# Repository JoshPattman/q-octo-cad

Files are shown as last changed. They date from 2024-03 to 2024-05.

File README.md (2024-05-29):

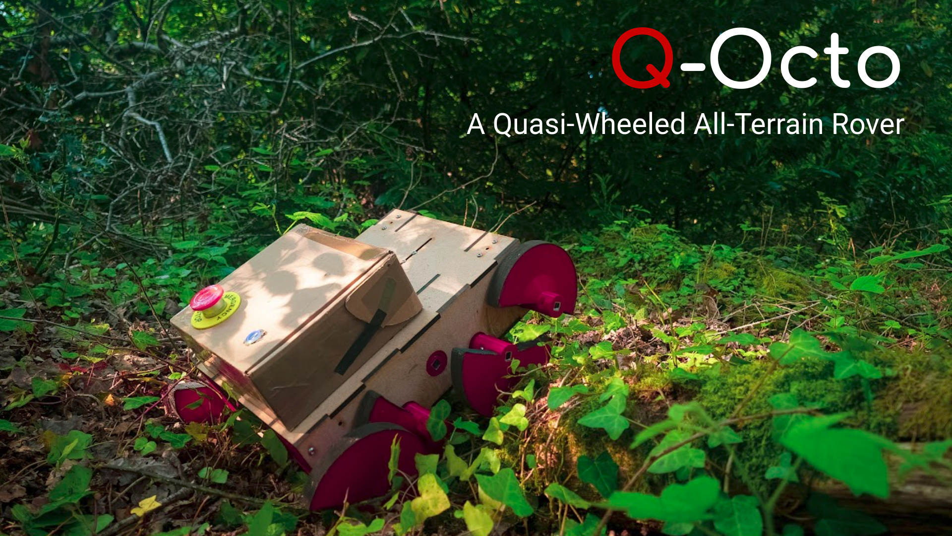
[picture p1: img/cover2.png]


# Q-Octo CAD
This Repo is the official home of the design of the Q-Octo robot! All CAD is using `FreeCAD Link Branch 2024-01-23`, but STL and DXF files are also provided.

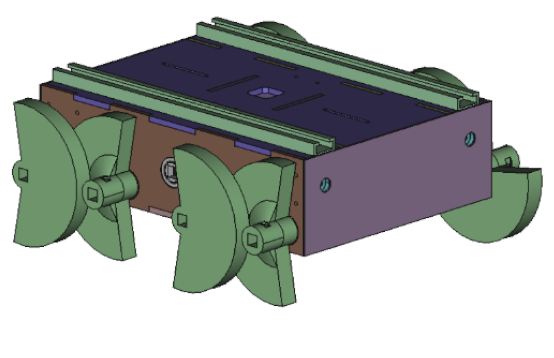
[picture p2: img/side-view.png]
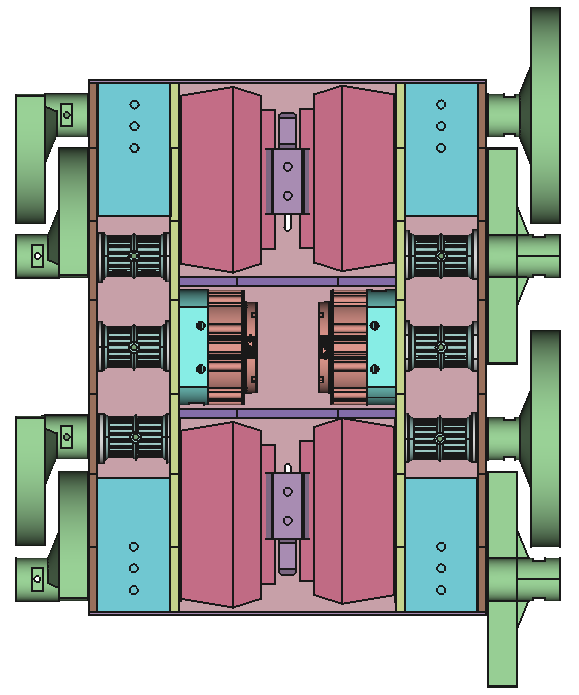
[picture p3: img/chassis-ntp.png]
 

## About Q-Octo
[Q-Octo](https://www.youtube.com/watch?v=2PIdxYJO_Ck) is an eight-quasi-wheeled robotics platform. It is designed to excel at forest traversal, easily being able to clamber over small logs and rocks due to its uniquely shaped wheels. However, due to each pair of neighboring wheels being 180 degrees out of phase, the robot can run smoothly as if it had circular wheels when on flat ground.

Q-Octo uses a pair of [CyberGear MicroMotors](https://www.aliexpress.com/item/1005005997659365.html), which provide not only high torque and speed but also feedback such as current amp draw and position. To power the motors, 4 [Parkside X20V](https://parkside-diy.com/gb/battery-technology/x20v-team) drill batteries are used, providing 6-hour continuous runtime paired with robust and safe recharging.

To build a Q-Octo, both a 3D printer and a laser cutter are required. It is sufficient to manufacture all 3D printed parts out of [Esun PLA+](https://www.esun3d.com/pla-pro-product/), providing excellent durability. All laser-cut parts (*except the front and rear battery cover) can be cut from 6 mm thick plyboard, which provides adequate rigidity and durability, assuming it is coated in outdoor paint.

## File Structure
- `cad/part/`: Contains all part files
- `cad/asm/`: Contains assembly files, using parts from `cad/part/`
- `mf/3d-print`: Contains all `stl` files ready for 3D printing
- `mf/lasercut`: Contains `dxf` files for laser-cutting

## Parts List _(Incomplete at current time)_

### Parts to Purchase
> These are just the mechanical parts for building the chassis. All of the control electronics can be found in the electronic repo.
- 2x CyberGear MicroMotor (Robot Dog Motor)
- 12mm Square Tube, Aluminum, Hollow (~1 meter, you need to cut it yourself)
- Assorted M4 bolts, ideally low profile
- M4 threaded inserts, diameter 5.6mm
- 20x 61704 ball bearings (20x27x4mm)
- 4x 5mm HTD belts 285mm length, 15mm wide
- 4x 5mm HTD belts 225mm length, 15mm wide
- 4x Parkside X20V drill battery

### Parts to Lasercut
> All parts should be lasercut from a 6mm wide material (unless otherwise specified), plyboard should be strong enough. It is recommended not to use acrylic as it can be brittle.
- 2x dxf/ChassisInnerPlate.dxf
- 2x dxf/ChassisOuterPlate.dxf
- 1x dxf/ChassisUpperPlate.dxf
- 1x dxf/ChassisLowerPlate.dxf
- 2x dxf/ChassisMotorSplashPlate.dxf
- 2x dxf/ChassisBatterySplashPlate.dxf (Cut this from thinner material, the thinner the better as it is not structural)

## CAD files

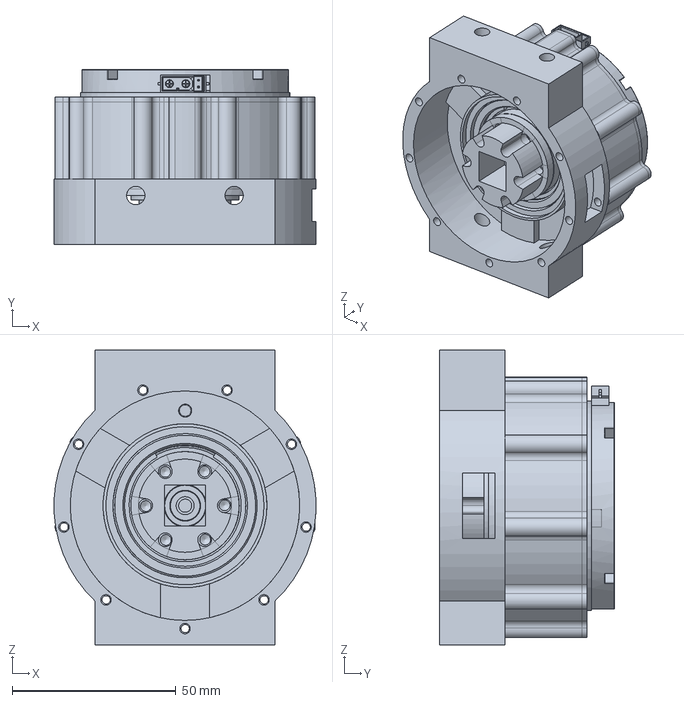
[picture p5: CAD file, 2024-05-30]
cad/asm/mounted-motor.FCStd
79.9 x 53.5 x 90.0 mm

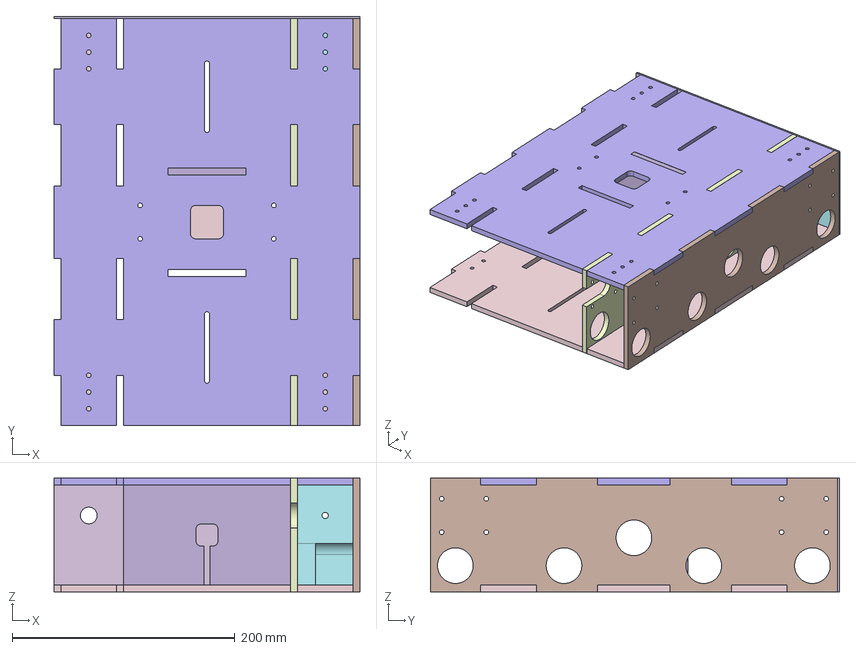
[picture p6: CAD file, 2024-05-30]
cad/part/chassis.FCStd
274.3 x 367.0 x 102.0 mm
LowerPlate
UpperPlate
OuterPlate
InnerPlate
PulleyBrace
MotorSplashPlate
BatterySplashPlate

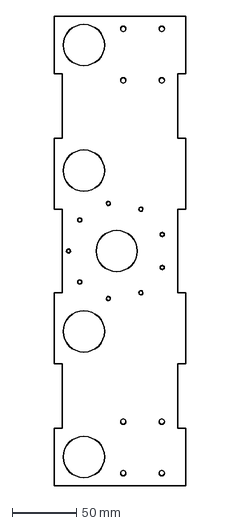
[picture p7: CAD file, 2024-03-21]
dxf/ChassisInnerPlate.dxf
102.0 x 365.0 mm

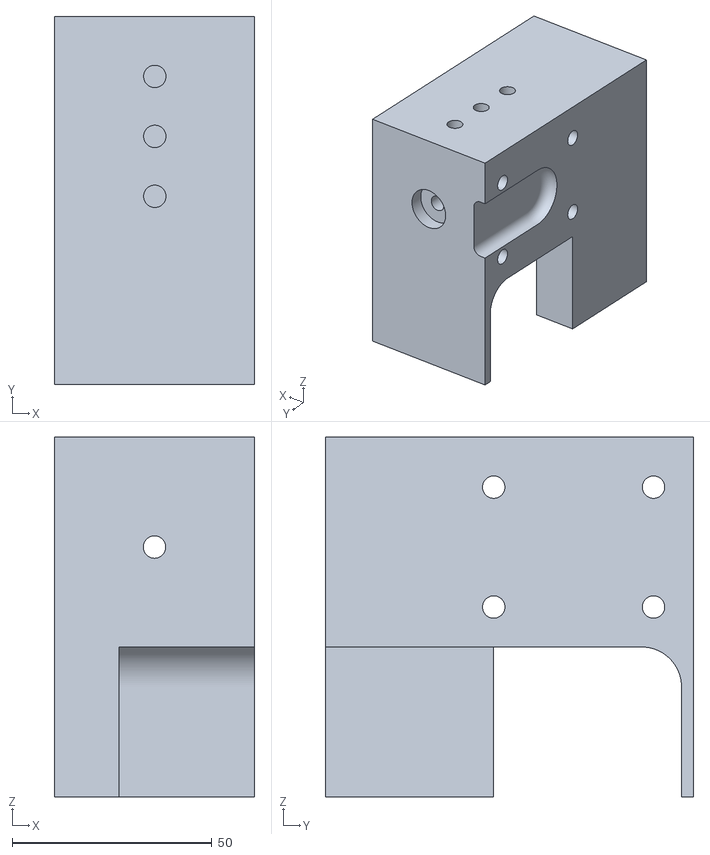
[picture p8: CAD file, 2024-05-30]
mf/3d-print/PulleyBrace.stl
50.1 x 92.1 x 90.0

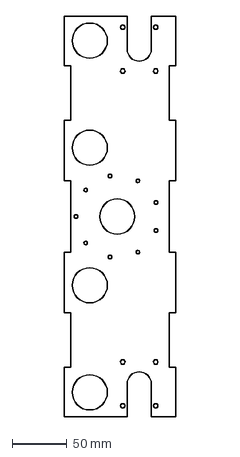
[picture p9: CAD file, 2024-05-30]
mf/lasercut/InnerPlate.dxf
102.0 x 365.0 mm

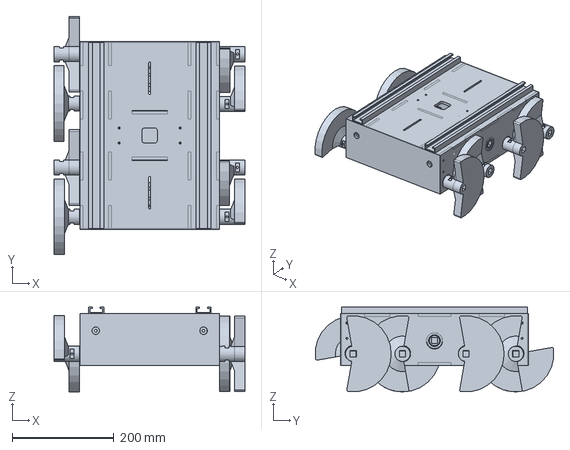
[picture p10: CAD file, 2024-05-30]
cad/asm/robot.FCStd
375.8 x 469.1 x 167.1 mm

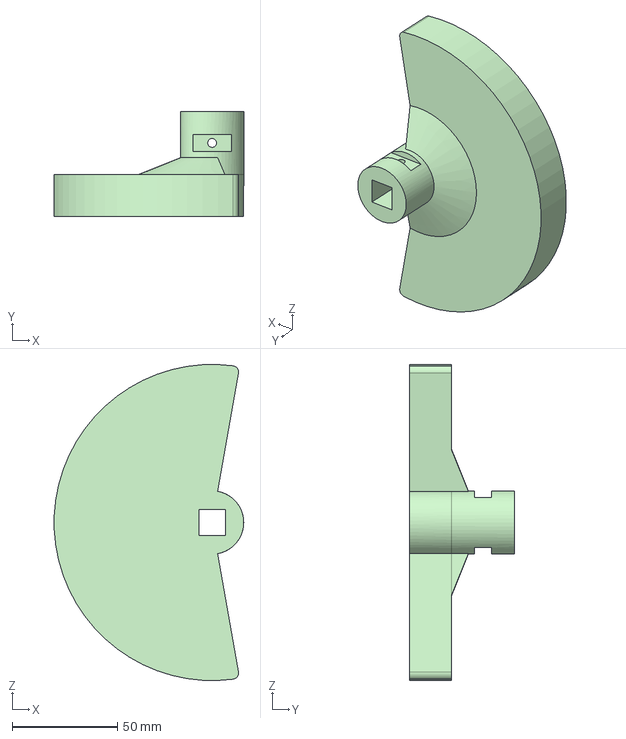
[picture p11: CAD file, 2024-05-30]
cad/part/wheel.FCStd
89.9 x 50.0 x 149.9 mm

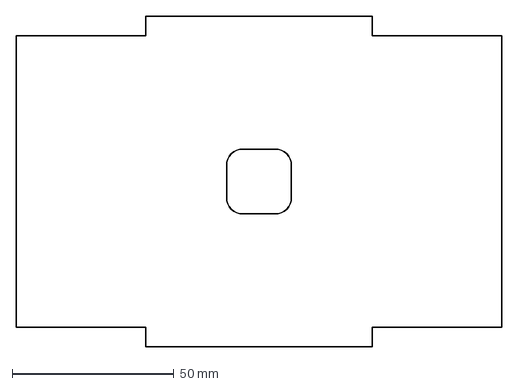
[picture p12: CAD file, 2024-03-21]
dxf/ChassisMotorSplashPlate.dxf
150.0 x 102.0 mm

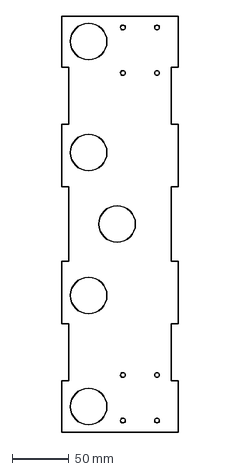
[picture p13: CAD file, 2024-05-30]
mf/lasercut/OuterPlate.dxf
102.0 x 365.0 mm

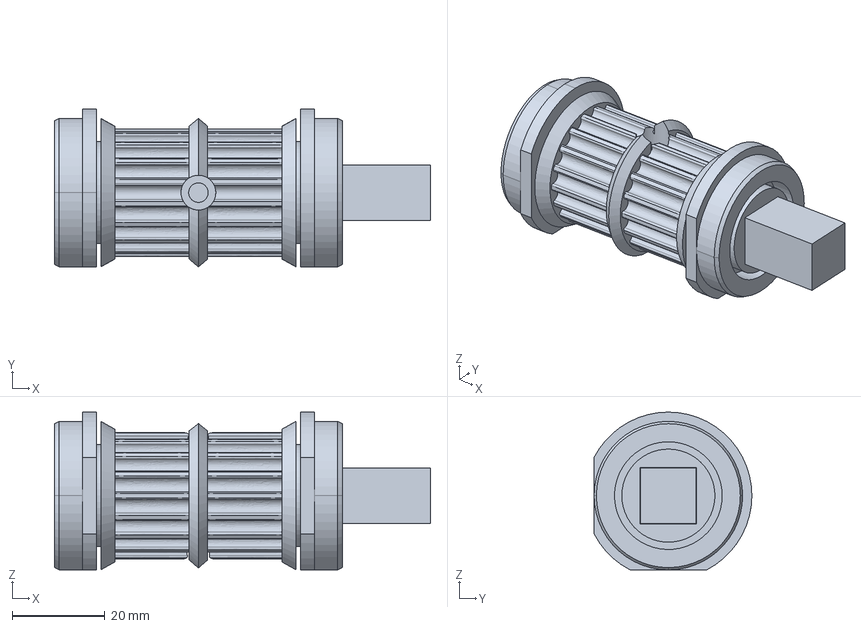
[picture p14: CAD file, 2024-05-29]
cad/asm/pulley.FCStd
81.0 x 34.0 x 34.0 mm

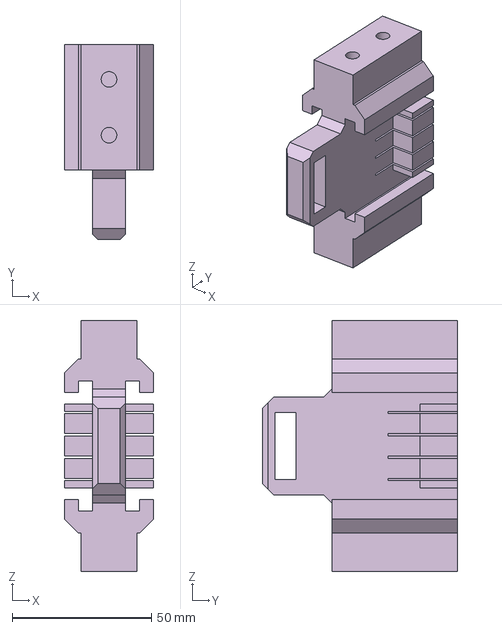
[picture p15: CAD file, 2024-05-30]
cad/part/battery-mount.FCStd
32.0 x 70.0 x 90.0 mm

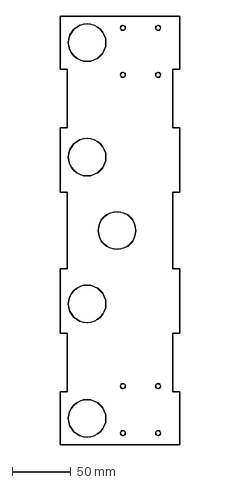
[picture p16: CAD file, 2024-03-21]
dxf/ChassisOuterPlate.dxf
102.0 x 365.0 mm

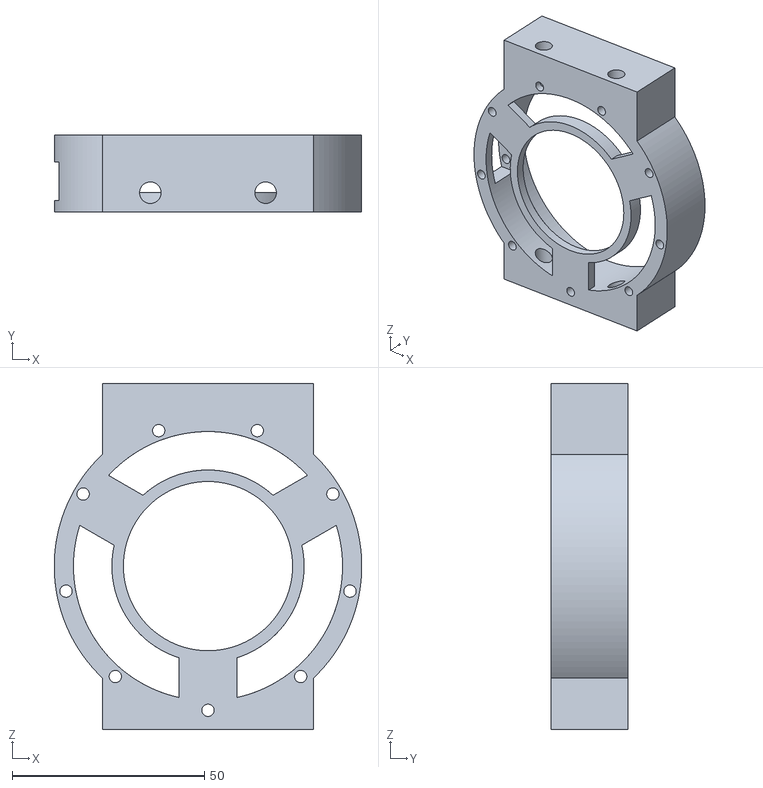
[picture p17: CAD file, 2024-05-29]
mf/3d-print/Mount.stl
80.0 x 20.0 x 90.0

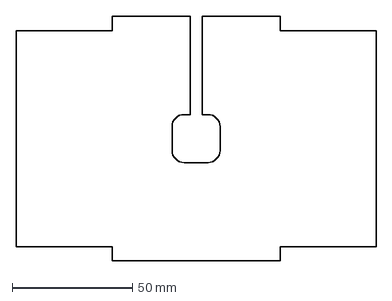
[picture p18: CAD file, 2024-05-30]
mf/lasercut/MotorSplashPlate.dxf
150.0 x 102.0 mm

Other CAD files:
mf/3d-print/Wheel.stl
cad/part/t-track.FCStd
dxf/ChassisLowerPlate.dxf
mf/3d-print/OuterBearingCasing.stl
cad/part/motor-mount.FCStd
cad/part/motor.FCStd
cad/part/parkside-x20v.FCStd
cad/part/payload-box-example.FCStd
cad/part/pulley.FCStd
dxf/ChassisUpperPlate.dxf
mf/3d-print/BatteryMount.stl
mf/3d-print/Coupler.stl
mf/3d-print/InnerBearingCasing.stl
mf/3d-print/Pulley.stl
mf/lasercut/BatterySplashPlate.dxf
mf/lasercut/LowerPlate.dxf
mf/lasercut/UpperPlate.dxf
v0.3/dxf/InnerPlate.dxf
v0.3/dxf/LowerPlate.dxf

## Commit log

2024-02-22 Added a waterproof box
    [waterproof-box.FCStd]
2024-02-22 Created a robot assembly file
    [asm-robot.FCStd]
2024-02-23 Added some lasercut rack assembly
    [asm-rack.FCStd, asm-robot.FCStd, motor-rack.FCStd]
2024-02-23 Added some wheels
    [asm-rack.FCStd, asm-robot.FCStd, battery.FCStd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]
2024-02-23 Added some drive shaft stuff
    [asm-rack.FCStd, asm-robot.FCStd, asm-shaft-support.FCStd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]
2024-02-23 more drive shaft stuff, but im gonna redo it
    [asm-rack.FCStd, asm-robot.FCStd, asm-shaft-support.FCStd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]
2024-02-23 Much better pulley
    [asm-rack.FCStd, asm-robot.FCStd, asm-shaft-support.FCStd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]
2024-02-28 whatever i did
    [asm-rack.FCStd, asm-robot.FCStd, asm-wheel-pulley.FCStd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]
2024-02-29 added motor mounts
    [asm-rack.FCStd, asm-robot.FCStd, motor-rack.FCStd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]
2024-03-06 Updated the new wheel pulley
    [asm-wheel-pulley.FCStd, part-wheel-pulley.FCStd]
2024-03-06 Calculated the diameter of the pulley
    [part-wheel-pulley.FCStd]
2024-03-06 Added some belt sizing
    [dia-belt.FCStd]
2024-03-06 cleaned up file
    [dia-belt.FCStd]
2024-03-06 A lot of cad on the body
    [asm-base.FCStd, asm-robot.FCStd, asm-wheel-pulley.FCStd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]
2024-03-06 big batty
    [asm-base.FCStd, asm-robot.FCStd, part-lasercut-rack.FCStd]
2024-03-07 Fixed incrorect placement
    [asm-base.FCStd, asm-robot.FCStd, asm-wheel-pulley.FCStd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]
2024-03-07 updates to asm
    [asm-base.FCStd, asm-robot.FCStd, motor.FCStd]
2024-03-07 updated to use double supports for pulleys
    [asm-base.FCStd, asm-robot.FCStd, asm-wheel-pulley.FCStd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]
2024-03-07 Added motor covers
    [asm-base.FCStd, asm-robot.FCStd, part-lasercut-rack.FCStd]
2024-03-07 added shorter drive shafts
    [asm-base.FCStd, asm-robot.FCStd, asm-wheel-pulley.FCStd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]
2024-03-08 Finished pr2?
    [asm-base.FCStd, asm-robot.FCStd, asm-wheel-pulley.FCStd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]
2024-03-11 flipped wheels
    [asm-base.FCStd, asm-robot.FCStd, asm-wheel-pulley.FCStd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]
2024-03-11 Dramatic skrinking
    [asm-base.FCStd, asm-robot.FCStd, asm-wheel-pulley.FCStd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]
2024-03-12 shrink the pulleys
    [asm-base.FCStd, asm-robot.FCStd, asm-wheel-pulley.FCStd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]
2024-03-12 Redid the assemblies, still not finished but its a lot nicer now
    [asm-base.FCStd, asm-pulley.FCStd, asm-robot.FCStd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]
2024-03-13 Thats the bulk of the new version. The bottom plate is still not attached though
    [asm-chassis.FCStd, asm-pulley.FCStd, part-battery.FCStd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]
2024-03-13 added a questionable way to mount lower to upper
    [asm-chassis.FCStd, part-chassis.FCStd]
2024-03-19 motor splash plates
    [asm-chassis.FCStd, asm-pulley.FCStd, part-chassis.FCStd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]
2024-03-19 Motor mounts
    [asm-chassis.FCStd, asm-pulley.FCStd, part-battery.FCStd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]
2024-03-19 Moved motor mount to seperate file
    [asm-chassis.FCStd, asm-pulley.FCStd, motor-mount.FCStd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]
2024-03-19 Cant remeber what i did
    [asm-chassis.FCStd, part-chassis.FCStd, t-track.FCStd]
2024-03-19 Added the mounting holes on the top plate
    [asm-chassis.FCStd, asm-pulley.FCStd, motor-mount.FCStd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]
2024-03-20 battery holder should now fit
    [DualBatteryHolder.stl, asm-chassis.FCStd, battery-connector.FCStd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]
2024-03-20 Modified battery holder to almost fit into chassis
    [DualBatteryHolder.stl, battery-connector.FCStd, motor-mount.FCStd]
2024-03-20 Switched to threaded inserts for 3d printed parts
    [motor-mount.FCStd, part-chassis.FCStd]
2024-03-20 Almotst done! Switched everything to threaded inserts, strengthened body, and redid assembly. Just need to add dust plates now
    [asm-chassis.FCStd, battery-connector.FCStd, motor-mount.FCStd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]
2024-03-20 Added a hole for wires in top plate
    [asm-chassis.FCStd, part-chassis.FCStd]
2024-03-20 square hole
    [asm-chassis.FCStd, battery-connector.FCStd, motor-mount.FCStd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]
2024-03-20 turns out you need to rotate the sketch for it to be correct
    [InnerPlate.dxf, LowerPlate.dxf, asm-chassis.FCStd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]
2024-03-21 Upgrade body to have larger amounts of material underneath the pulleys
    [asm-chassis.FCStd, asm-pulley.FCStd, motor-mount.FCStd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]
2024-03-21 Added a chanfer to battery holder for quick reload
    [asm-chassis.FCStd, battery-connector.FCStd]
2024-03-21 thickened one peice and added a little tolerance
    [asm-chassis.FCStd, part-chassis.FCStd]
2024-03-21 Exported dxfs for laser cutting
    [ChassisInnerPlate.dxf, ChassisLowerPlate.dxf, ChassisMotorSplashPlate.dxf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]
2024-03-21 Increase motor mount hole size
    [ChassisInnerPlate.dxf, part-chassis.FCStd]
2024-03-21 Added a parts list
    [asm-chassis.FCStd]
2024-03-21 Cleaned up file structure
    [ChassisInnerPlate.dxf, ChassisLowerPlate.dxf, ChassisMotorSplashPlate.dxf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]
2024-03-21 not sure what i did
    [asm-chassis.FCStd]
2024-04-23 added the motor part with motor mount
    [part-motor-with-mount.FCStd]
2024-04-24 less moronic pulleys
    [asm-chassis.FCStd, asm-pulley.FCStd, part-wheel-pulley.FCStd]
2024-04-25 upgrade parts to new split design
    [Pulley.stl, Washer.stl]
2024-04-25 Better Pulley
    [part-wheel-pulley.FCStd]
2024-04-25 stl files for new pulley
    [BearingSeat.stl, Pulley.stl, Washer.stl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]
2024-04-29 fixed pulleys
    [asm-chassis.FCStd, asm-pulley.FCStd, part-wheel-pulley.FCStd]
2024-04-29 improved motor mount
    [asm-chassis.FCStd, motor-mount.FCStd, part-motor-with-mount.FCStd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]
2024-04-29 Upgrades people upgrades
    [Coupler.stl, Mount.stl, asm-chassis.FCStd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]
2024-05-01 stl update washer
    [Washer.stl]
2024-05-02 upgrades to motor coupler
    [Coupler.stl, asm-chassis.FCStd, asm-motor.FCStd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]
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2024-05-10 added motor to chassis
    [asm-chassis.FCStd, asm-motor.FCStd]
2024-05-13 Update tolerance of some parts
    [BearingSeat.stl, Washer.stl, part-wheel-pulley.FCStd]
2024-05-13 reorganise into folder-assemblies are broken rn
    [battery-mount.FCStd, chassis.FCStd, motor-mount.FCStd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]
2024-05-13 Renaming and fixing some stuff
    [battery-mount.FCStd, chassis.FCStd, motor-mount.FCStd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]
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2024-05-29 Added all stl and dxf
    [BatteryMount.stl, BatterySplashPlate.dxf, Coupler.stl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]
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2024-05-30 Added a slot in motor splash and slightly increased space between pulleys and floor
    [InnerPlate.dxf, MotorSplashPlate.dxf, OuterPlate.dxf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]
